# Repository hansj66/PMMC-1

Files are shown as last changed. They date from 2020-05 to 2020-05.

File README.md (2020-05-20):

# PMMC-1
Poor Man's Machine Crawler mk I

The PMMC-1 is an eight legged walking robot based on the Automaton robot controller.

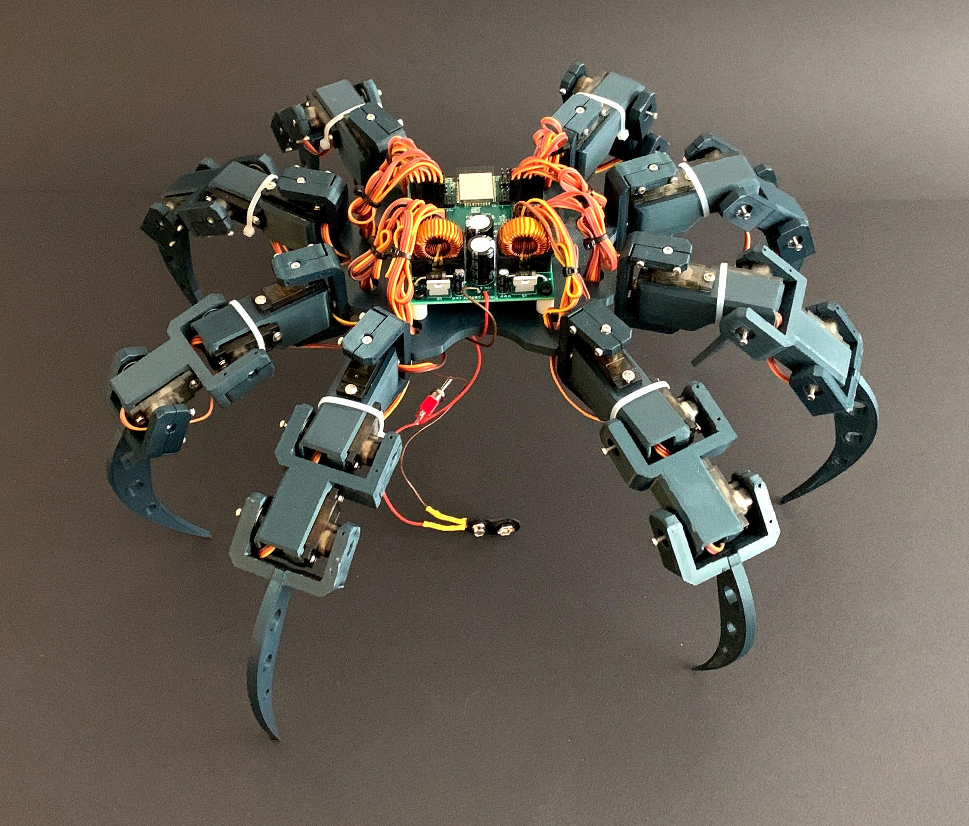
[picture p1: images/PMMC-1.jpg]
PMMC-1


# Bill of Materials

* Automaton controller board
* 24 x MG90S servos
* 24 x 604ZZ ball bearings
* 48 x 13mm M2 screws
* 24 x M2 8-10mm screws
* PTFE tubing
* 3D printed parts (STEP files in this repo)
* 3 x 10mm nylon spacers
* 3 x M3 screws
* zip ties

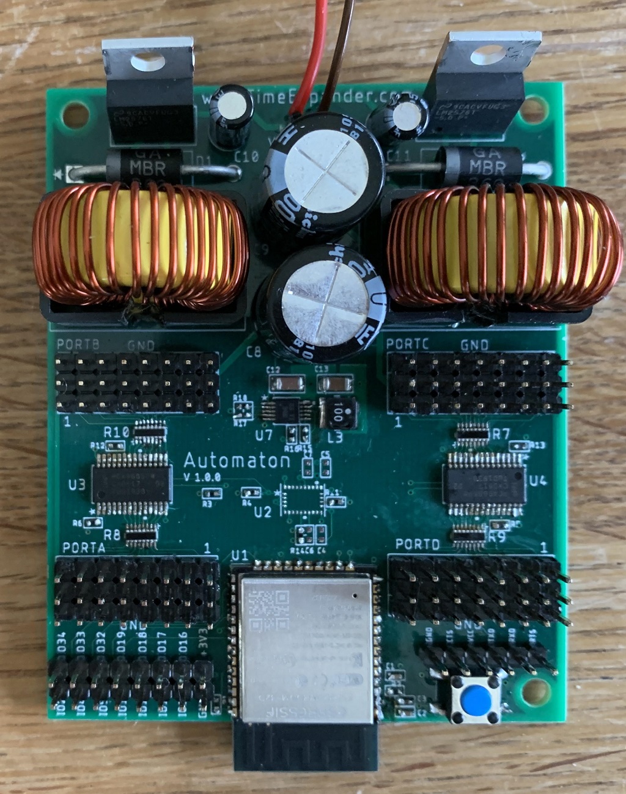
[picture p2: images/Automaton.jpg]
Automaton robot controller


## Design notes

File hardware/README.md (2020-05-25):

# Programming and debugging

In order to connect to a network, "WIFI_SSID" and "WIFI_PASS" has to be defined as environment 
variables (including quotes) before building the project

Connect a FTDI cable to the 6 pin programming header. Make sure to get the orientation right or you will risk frying the board (Black wire is Gnd).

The board can be programmed using [PlatformIO](https://platformio.org/). Just open the project the firmware folder in PiO and build.

1. Press and hold down the button while switching on power to enter programming mode. 
1. Then press the "upload" button on the PiO toolbar to program the board

# Calibration

The robot is running a webserver where you can do zero calibration of servos and also create poses for saving in the robot's non volatile memory (4k available).

After power on, the robot will connect you your SSID using the credentials provided in the environment variables. It then announces the web server name on the network using mDNS.

Open a web browser on a device connected to the same network and open the configuration page:

Your servos will probably not be in the neutral position out of the box. Attach one servo at a time. Enable the servo by ticking the corresponding "enable" box. Then use the slider to adjust the servo to the desired neutral position.

After all the servos has been calibrated, press the save button. This will save the parameters in non volatile memory and be used as default startup parameters on the next boot.

http://pmmc-1/

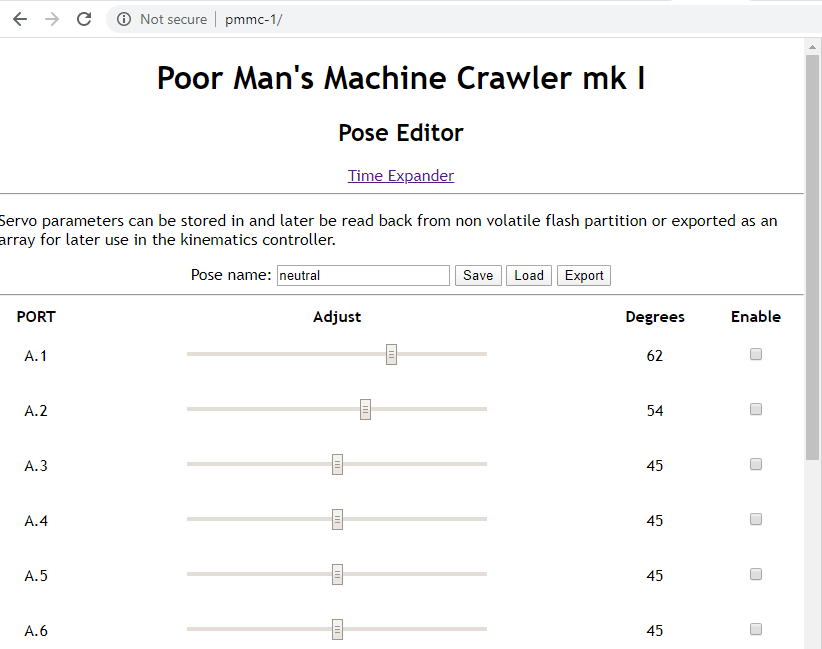
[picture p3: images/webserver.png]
Configuration page


The same web server exposes a simple API that allows you to manipulate the servos in order to create poses. These poses can then be associated with a key and stored in NV memory.

# Recommended Servo wiring

(ESP pointing north. Counting clockwise)

## Function Port

TBD

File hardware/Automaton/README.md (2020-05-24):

# Automaton robot controller

(This board is still in development)

The Automaton is a 32 channel servo controller with an onboard 9DOF sensor fusion IMU. 

This repo only contains gerber / drill files and assembly information (no design files). The gerber files can be uploaded to any PCB manufacturer.

The board is a 4 layer board. Stackup is .GTL .G1 .G2 .GBL

A detailed description of the board can be found [here](https://www.timeexpander.com/posts/servoboard/)

Automaton robot controller

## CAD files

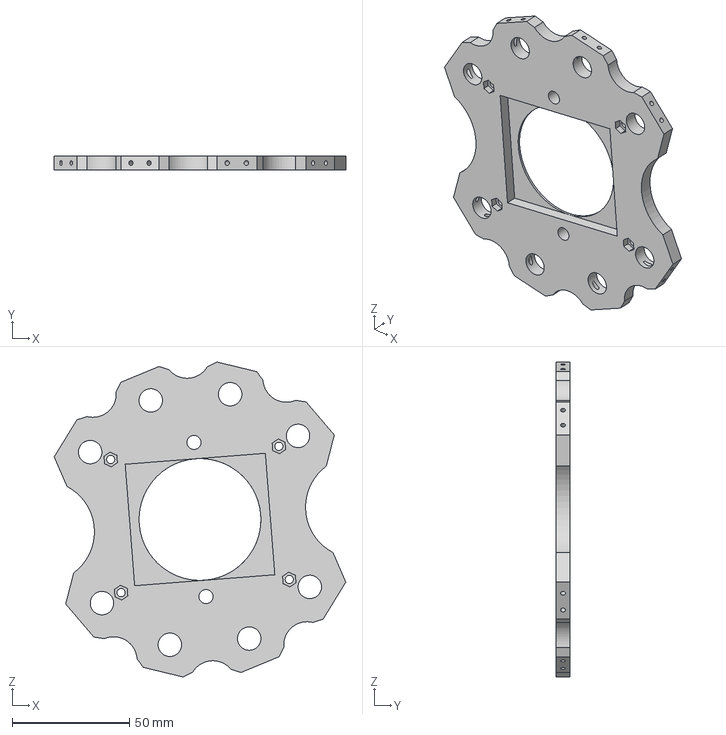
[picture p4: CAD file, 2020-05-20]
hardware/STEP/body.step
124.5 x 6.00 x 134.4 mm

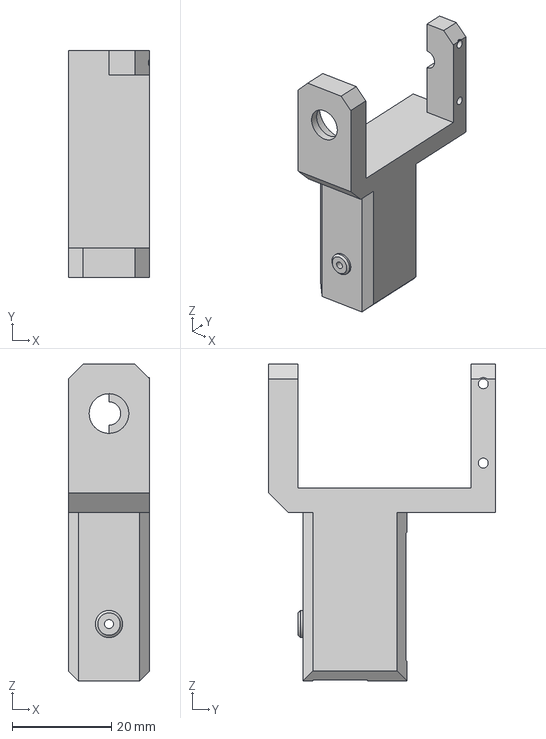
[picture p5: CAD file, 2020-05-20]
hardware/STEP/knee_joint.step
16.4 x 45.9 x 64.0 mm

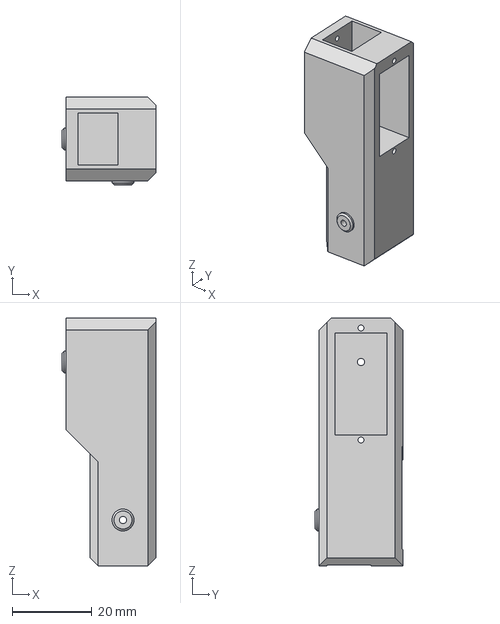
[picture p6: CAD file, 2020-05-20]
hardware/STEP/hip_servo.step
23.4 x 22.0 x 62.0 mm

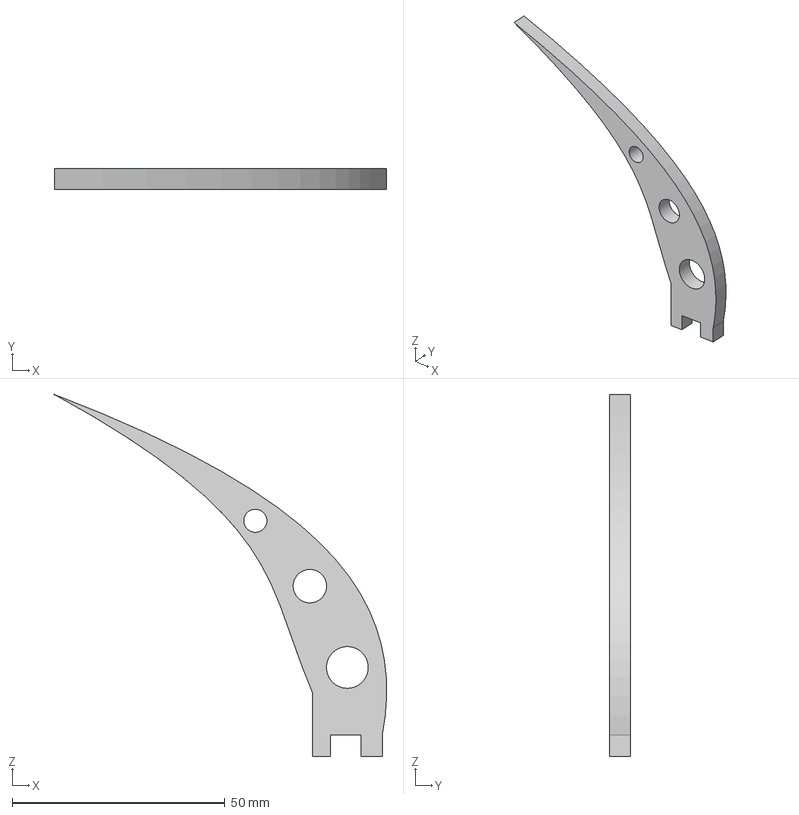
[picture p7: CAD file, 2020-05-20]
hardware/STEP/claw.step
78.0 x 5.00 x 85.0 mm

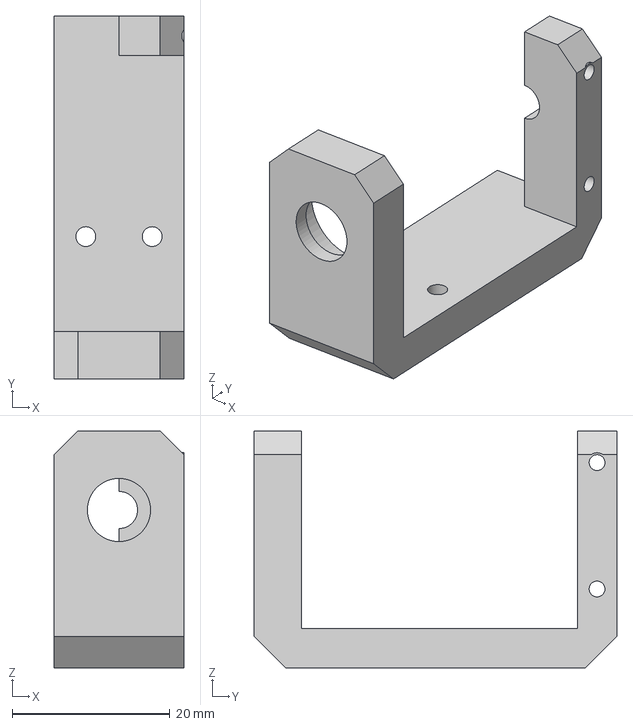
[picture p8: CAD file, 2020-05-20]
hardware/STEP/hip_joint.step
16.4 x 45.9 x 30.0 mm

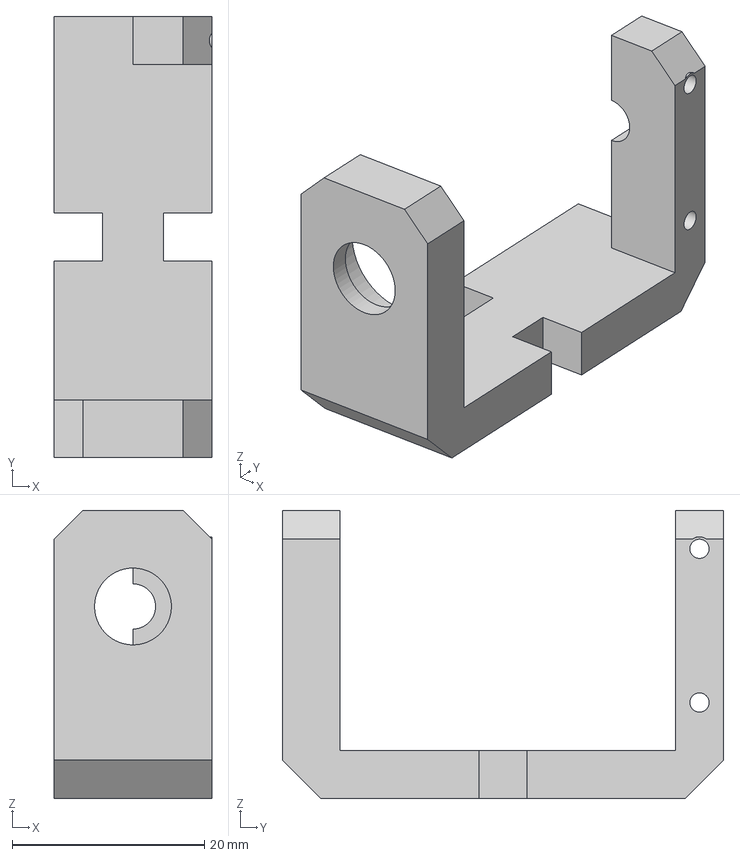
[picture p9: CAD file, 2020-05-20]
hardware/STEP/ankle_joint.step
16.4 x 45.9 x 30.0 mm

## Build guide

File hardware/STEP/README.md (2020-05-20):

# PMMC-1

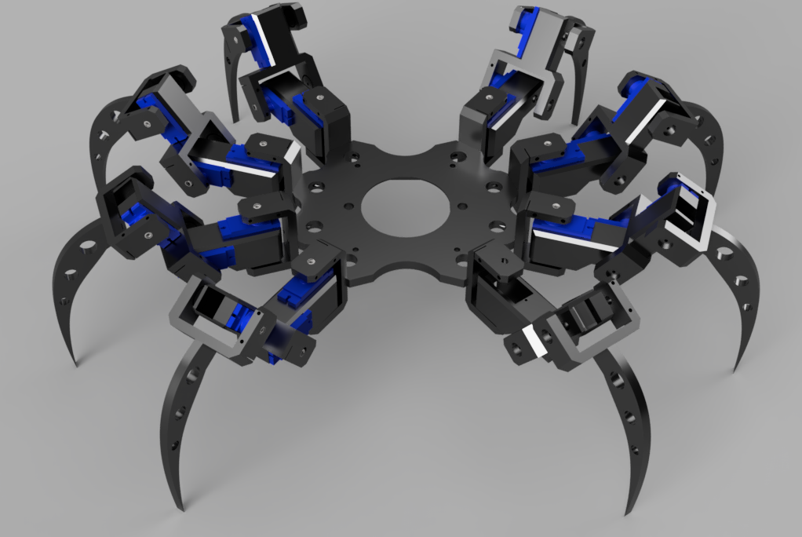
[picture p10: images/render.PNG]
Render


# 3D printed parts

* 1 x body.step
* 8 x hip_joint.step
* 8 x hip_servo.step
* 8 x knee_joint.step
* 8 x ankle_joint.step
* 8 x claw.step
* 24 x clamp.step

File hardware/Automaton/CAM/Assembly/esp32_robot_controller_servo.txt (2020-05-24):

Partlist exported from C:/Users/hansj/Documents/EAGLE/projects/ESP32_ROBOT_CONTROLLER_SERVO/esp32_robot_controller_servo.sch at 5/1/2020 7:43 PM

Qty Value                Device                              Package                   Parts                                      Description BUILT_BY    COPYRIGHT                                                   MANUFACTURER      MANUFACTURER_PART_NUMBER VALUE VENDOR           
1   0.0068uF             CAPACITOR0402                       CAP_0402                  C7                                                                                                                                                                                               
1   0.12uF               CAPACITOR0402                       CAP_0402                  C5                                                                                                                                                                                               
3   0.1uF                CAPACITOR0402                       CAP_0402                  C3, C4, C6                                                                                                                                                                                       
1   100k                 RESISTOR                            RES_0402                  R16                                                                                                                                                                                              
2   10V/100uF            ELECTROLYTIC_CAPACITORNICHICON_5    NICHICON_UHE1A101MDD1TD   C10, C11                                                                                                                                                                                         
10  10k                  RESISTOR                            RES_0402                  R1, R2, R3, R4, R5, R6, R11, R12, R13, R14                                                                                                                                                       
2   10uF                 CAPACITOR0402                       CAP_0402                  C1, C2                                                                                                                                                                                           
1   10uF                 CAPACITOR1206                       CAP_1206                  C12                                                                                                                                                                                              
1   10uH                 INDUCTOR_VLCF4024T-100MR90-2        IND_4028                  L3                                                                                                                                                                                               
1   130k                 RESISTOR                            RES_0402                  R15                                                                                                                                                                                              
2   1M                   RESISTOR                            RES_0402                  R17, R18                                                                                                                                                                                         
4   220                  EXB-2HV221JVEXB2HV-M                EXB2HV-M                  R7, R8, R9, R10                                        EMA_UL_Team                                                                               EXB-2HV221JV                   Panasonic        
1   22uF                 CAPACITOR1206                       CAP_1206                  C13                                                                                                                                                                                              
2   25V/1000uF           ELECTROLYTIC_CAPACITORNICHICON_12_5 NICHICON_UHE1E102MHD6     C8, C9                                                                                                                                                                                           
1   BATTERY              POWER_SOLDER_TERMINAL9V             BATTERY_SOLDER_TERMINAL   J6                                                                                                                                                                                               
1   BNO055               BNO055                              QFN_BNO055                U2                                                     EMA_Matt    Copyright (C) 2018 Accelerated Designs. All rights reserved                   BNO055                         Bosch            
1   ESP-WROOM-32D        ESP-WROOM-32D                       ESP_WROOM_32D             U1                                                                                                                                                                                               
1   ESP_ROBOT_BOARD_GPIO ESP_ROBOT_BOARD_GPIO                ESP_ROBOT_BOARD_GPIO      U$1                                                                                                                                                                                              
1   FTDI_CONNECTOR       FTDI_CONNECTOR                      FTDI_CONNECTOR            J1                                                                                                                                                                                               
2   LM2576T-5.0/NOPB     LM2576T-5.0/NOPB                    T05B                      U5, U6                                                                                                                                                                                           
1   LOGO_SELFIE          LOGO_SELFIE                         LOGO_SELFIE               U$2                                                                                                                                                                                              
2   MBR360RLG            MBR360RLG                           DO-201AD                  D1, D2                                                 EMA_UL_Team                                                                               MBR360RLG                      ON Semiconductor 
2   PCA9685PW            PCA9685PWSOT361-1-M                 SOT361-1-M                U3, U4                                                 EMA_UL_Team                                                                               PCA9685PW                      NXP              
2   PE-92108             INDUCTOR_PE-92108                   INDUCTOR_PE-92108         L1, L2                                                                                                                                                                                           
4   RC_SERVO_HEADER_X8   RC_SERVO_HEADER_X8                  RC_SERVO_HEADER_X8        PORTA, PORTB, PORTC, PORTD                                                                                                                                                                       
1   SWITCH_PTS645        SWITCH_PTS645                       SWITCH_PTS645_EE_NBIOT_01 S1                                                                                                                                                                                               
1   TPS62056DGSRDGS10-M  TPS62056DGSRDGS10-M                 DGS10-M                   U7                                                     EMA_UL_Team                                                             Texas Instruments TPS62056DGSR                   Texas Instruments

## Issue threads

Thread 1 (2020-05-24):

Check for existence of "neutral" profile on boot

hansj66, 2020-05-24:
If it doesn't exist, disable all servos. If it has been created, then enable servos and update active pwm profile.

Closed 2020-05-25.

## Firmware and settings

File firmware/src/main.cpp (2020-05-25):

/*
*  Copyright [2020] [Hans Jørgen Grimstad]
*  
*  Licensed under the Apache License, Version 2.0 (the "License");
*  you may not use this file except in compliance with the License.
*  You may obtain a copy of the License at
*  
*      http://www.apache.org/licenses/LICENSE-2.0
*  
*  Unless required by applicable law or agreed to in writing, software
*  distributed under the License is distributed on an "AS IS" BASIS,
*  WITHOUT WARRANTIES OR CONDITIONS OF ANY KIND, either express or implied.
*  See the License for the specific language governing permissions and
*  limitations under the License.
*/

#include <ESPmDNS.h>
#include <Arduino.h>
#include <WiFi.h>
#include <AsyncTCP.h>
#include <ESPAsyncWebServer.h>
#include <ArduinoNvs.h>
#include <wire.h>
#include "automaton.h"

extern String config_page;

AsyncWebServer server(80);
Automaton automaton;

void notFound(AsyncWebServerRequest *request) 
{
    request->send(404, "text/plain", "Not found");
}


void setup() 
{
    Serial.begin(115200);


    // Initialize the servo controller
    automaton.begin();

    // Initialize non volatile storage for servo parameters
    NVS.begin();

    // Make discovery on the network somewhat easier than having to rely on the IP address.
    // Just visit http://PMMC-1 after boot in order to configure the servos or create poses
    if (!MDNS.begin("PMMC-1"))
    {
        Serial.printf("Error starting mDNS!\n");
    }

    // Enable WiFi station mode. 
    WiFi.mode(WIFI_STA);

    // Connect to your access point
    // Note:    In order to connect to a network, "WIFI_SSID" and "WIFI_PASS" has to be defined as environment 
    //          variables (including quotes) before building the project. Alternatively SSID and password 
    //          can be passed as hard coded  string arguments to WiFi.begin().
    WiFi.begin(WIFI_SSID, WIFI_PASS);
    if (WiFi.waitForConnectResult() != WL_CONNECTED) 
    {
        Serial.printf("WiFi Failed!\n");
        return;
    }

    Serial.print("IP Address: ");
    Serial.println(WiFi.localIP());

    // Check for the existense of a neutral/zero pose in non volatile memory.
    // If it exists, we'll load it and update the corresponding servo positions.
    automaton.selectPose("neutral");

    // http://pmmc-1 will return the configuration page. This allows the user to interactively
    // manipulate servo positions, create poses and also store this
    server.on("/", HTTP_GET, [](AsyncWebServerRequest *request)
    {
        request->send(200, "text/html", config_page);
    });

    // Let's define some service endpoints.

    // 1) "trim" - Adjusts servo position according to corresponding slider in configuration page
    server.on("/trim", HTTP_GET, [] (AsyncWebServerRequest *request) 
    {
        String id;
        String pos;
        if (request->hasParam("id")) 
        {
            id = request->getParam("id")->value();
            Serial.printf("Servo ID: %s\n", id.c_str());
        } 
        if (request->hasParam("pos")) 
        {
            pos = request->getParam("pos")->value();
            Serial.printf("Servo position: %s\n", pos.c_str());
        } 

        automaton.trim(atoi(id.c_str()), atoi(pos.c_str()));
        request->send(200, "text/plain", "OK");
    });

    // 2) "save" - Stores all servo parameters in non volatile flash memory
    server.on("/save", HTTP_GET, [] (AsyncWebServerRequest *request) 
    {
        String servoParam;
        char servo[5];
        String poseName = "default";
        uint8_t parameterBlob[MAX_SERVO_NUM];

        if (request->hasParam("pose")) 
        {
            poseName = request->getParam("pose")->value();
        }

        for (int i=0; i<MAX_SERVO_NUM; i++)
        {
            sprintf(servo, "s%d", i);
            if (request->hasParam(servo)) 
            {
                servoParam = request->getParam(servo)->value();
                parameterBlob[i] = atoi(servoParam.c_str());
                // Serial.printf("Saving %d : %d\n", i, atoi(servoParam.c_str()));
            } 
        }

        // Write parameters to non volatile key value store 
        NVS.setBlob(poseName, parameterBlob, sizeof(parameterBlob));

        request->send(200, "text/plain", "OK");
    });

    // "load" - Reads all servo parameres associated with a given pose and updates
    //          the sliders in the configuration page accordingly
    server.on("/load", HTTP_GET, [] (AsyncWebServerRequest *request) 
    {
        String poseName;
        if (request->hasParam("pose")) 
        {
            poseName = request->getParam("pose")->value();
            Serial.printf("Pose: %s\n", poseName.c_str());
        }

        // read from flash
        size_t blobLength = NVS.getBlobSize(poseName);   
        Serial.printf("Size of %s pose: %d\n", poseName.c_str(), blobLength);

        uint8_t parameterBlob[MAX_SERVO_NUM];
        NVS.getBlob(poseName, parameterBlob, sizeof(parameterBlob));
        String responseData;
        for (int i=0; i<MAX_SERVO_NUM; i++)
        {
            Serial.printf("Loaded: s%d : %u\n", i, parameterBlob[i]);
            responseData += String(parameterBlob[i]);
            if (i < MAX_SERVO_NUM-1)
                responseData += " ";
        }

        request->send(200, "text/html", responseData);
    });

        // 1) "trim" - Adjusts servo position according to corresponding slider in configuration page
    server.on("/enable", HTTP_GET, [] (AsyncWebServerRequest *request) 
    {
        String id;
        String enable;
        if (request->hasParam("id")) 
        {
            id = request->getParam("id")->value();
            Serial.printf("Enable servo ID: %s\n", id.c_str());
        } 
        if (request->hasParam("enable")) 
        {
            enable = request->getParam("enable")->value();
            Serial.printf("Enabled: %s\n", enable.c_str());
        } 

        bool bEnable = strcmp(enable.c_str(), "false");
        automaton.enable(atoi(id.c_str()), bEnable);
        request->send(200, "text/plain", "OK");
    });



    server.onNotFound(notFound);
    server.begin();
}

void loop() 
{
}

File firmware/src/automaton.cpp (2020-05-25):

/*
*  Copyright [2020] [Hans Jørgen Grimstad]
*  
*  Licensed under the Apache License, Version 2.0 (the "License");
*  you may not use this file except in compliance with the License.
*  You may obtain a copy of the License at
*  
*      http://www.apache.org/licenses/LICENSE-2.0
*  
*  Unless required by applicable law or agreed to in writing, software
*  distributed under the License is distributed on an "AS IS" BASIS,
*  WITHOUT WARRANTIES OR CONDITIONS OF ANY KIND, either express or implied.
*  See the License for the specific language governing permissions and
*  limitations under the License.
*/

#include <Arduino.h>
#include <Wire.h>
#include <Adafruit_PWMServoDriver.h>
#include <ArduinoNvs.h>
#include "automaton.h"

Adafruit_PWMServoDriver driver_A(0x41);
Adafruit_PWMServoDriver driver_B(0x42);

Automaton::Automaton() 
{
    // Initialize pwm parameter array to a default mid level 
    // This will have to be tuned in the configuration settings later.
    for (int i : _pwm)
    {
        _pwm[i] = SERVO_MID;
        _enable[i] = true;
    }
}

void Automaton::begin()
{
    // Initialize the wire library (necessary for I2C)
    Wire.begin(GPIO_NUM_21, GPIO_NUM_22);
    // Initialize the Adafruit driver for each of the onboard PCA9685 PWM controllers
    driver_A.begin();
    driver_B.begin();
    driver_A.setOscillatorFrequency(25000000);
    driver_B.setOscillatorFrequency(25000000);
    driver_A.setPWMFreq(50);
    driver_B.setPWMFreq(50);

    // Initialize the GPIO pins that control the PCA9685 enable signals.
    pinMode(GPIO_NUM_23, OUTPUT);
    pinMode(GPIO_NUM_25, OUTPUT);
    digitalWrite(GPIO_NUM_23, LOW);
    digitalWrite(GPIO_NUM_25, LOW);

    disableAll();
}


void Automaton::disableAll()
{
    // This is not a "true" enable, since the servos will still have power.
    for (int i=0; i<16; i++)
    {
        driver_A.setPWM(i, 0, 4096);
        driver_B.setPWM(i, 0, 4096);
    }
}

void Automaton::enable(int servoId, bool enable)
{
    if ((servoId < 0) || (servoId > 31))
        return;

    _enable[servoId] = enable;

    Adafruit_PWMServoDriver * driver;
    int internalId = servoId;


    if (servoId < 16)
    {
        Serial.println("Enabling Driver A");
        driver = &driver_A;
    }
    else
    {
        Serial.println("Enabling Driver B");
        driver = &driver_B;
    }

    // Blame the braniac, who decided to make the schematic prettier...
    /*
    if (servoId < 8)
        internalId = 8-servoId-1;
    else if (servoId < 16)
        internalId = 16-servoId+7;
    else if (servoId < 24 )
        internalId = 8-(servoId-16)-1;
    else if (servoId < 32)
        internalId = 16-(servoId+7);
    */        
    if (servoId < 8)
        internalId = 7-servoId;
    else if (servoId < 16)
        internalId = 23-servoId;
    else if (servoId < 24 )
        internalId = 23-servoId;
     else if (servoId < 32)
        internalId = 31-servoId+8;    

        //23: -1 -8


     Serial.printf("ServoId: %d, Internal ID: %d (enabled: %d, pwm: %d)\n", servoId, internalId, enable, _pwm[servoId]);
    
    if (enable)
        driver->setPWM(internalId, 0, _pwm[servoId]);
    else
        driver->setPWM(internalId, 0, 4096);
}

void Automaton::trim(int servoId, int degrees)
{
    int pwm_count = (degrees*200) / 90 + SERVO_MIN;
    _pwm[servoId] = pwm_count;
    enable(servoId, _enable[servoId]);
}


void Automaton::selectPose(String name)
{
    uint8_t parameterBlob[MAX_SERVO_NUM];

    if (!NVS.getBlob(name.c_str(), parameterBlob, MAX_SERVO_NUM))
    {
        Serial.printf("ERROR: loading pose '%s' failed.\n", name.c_str());
    }
    Serial.printf("INFO: loaded pose '%s' ok.\n", name.c_str());
    for (int i=0; i<MAX_SERVO_NUM; i++)
    {
        _pwm[i] = parameterBlob[i];
        trim(i, _pwm[i]);
        _enable[i] = true;
        enable(i, _enable[i]);
    }

}

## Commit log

2020-05-20 Added render and STEP files
    [ankle_joint.step, body.step, claw.step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]
2020-05-24 Added gerber files
    [copper_bottom_l4.gbl, copper_top_l1.gtl, drill_1_16.xln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]
2020-05-24 Added code for pwm controller
2020-05-24 Added webserver info
    * fixed PWM frequeuncy (was 46.8Hz. is now 50Hz)
    * fixed configurable pulse length interval for 0-180 degree movement
    * fixed PWM disable function
    [automaton.cpp, config_page.cpp]
2020-05-25 Default profile and pin mapping
    * Fixed missing call to driver_B in Automaton::disableAll()
    * Fixed issue where ticking "enable" in configuration page wouldn't update the servo position according to the slider.
    * Now checking for the existense of a "neutral" profile after boot. If it exists, servo parameters will be loaded from this profile and servos are enabled. If it doesn't exist, the servos are disabled.
    * Now using a more intuitive 0-90 degree range in the gui. Automaton converts degrees to pwm_count in trim() method.
    * Fixed NVS loading of stored parameters via config page.
    * Updated screen shot of configuration page
    [automaton.cpp, automaton.h, config_page.cpp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]
